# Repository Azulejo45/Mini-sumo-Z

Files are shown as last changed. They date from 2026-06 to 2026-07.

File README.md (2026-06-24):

### ┍━━━━━━━━━━━━»•»  «•«━━━━┑
#   ┕Zangetsu-MiniSumo┙        

### - Proyecto de mini sumo con la capacidad de ser controlado de manera bluetooth y automata. Equipado con 4 sensores:  2 laterales, 1 frontal y uno en la parte inferior, el de piso.
♥

## ..••°°━✦❘༻⋞ 〈 Autores  〉 ⋟༺❘✦━━°°••..

- ⋆ˊˎ-   ┌──༺♥༻❀**Velazquez Joaquim**❀༺♥༻
  
- ⋆ˊˎ-  **Rodriguez Thiago**

### *---16/3/2026---*

♥
## •*¨*•.¸¸☆*･ﾟ Especificaciones generales ﾟ･*☆¸¸.•*¨*•

˚₊· ͟͟͞͞➳❥ Dimensiones del robot: 10 cm x 10 cm x 4,5 cm.

˚₊· ͟͟͞͞➳❥ Consumo total: 7,4V.

˚₊· ͟͟͞͞➳❥ Corriente total: 800mA.

˚₊· ͟͟͞͞➳❥ Material de la carrocería: PLA.

˚₊· ͟͟͞͞➳❥ Peso (aproximado): 300g.
## ✭∞∞∞∞∞∞∞∞✭∞∞•,¸,.·' ✩ '·.,¸,•∞∞✭∞∞∞∞∞∞∞∞✭

♥
## Objetivo del proyecto
### ✩°｡𓂃𓏧︶︶︶︶︶︶︶︶┈୨•♡•୧┈︶︶︶︶︶︶︶𓂃𓏧｡°✩
_El objetivo principal de este proyecto es poner a prueba lo aprendido en años anteriores y este, pudiendo aplicarlo en el proceso de preparacion y  creacion de un robot modelo Mini-Sumo, siguiendo el reglamento de la liga nacional de robotica LNR, para que se encuentre en condiciones en poder participar en una competencia de esta misma_
### ✩°｡𓂃𓏧⌒⌒⌒⌒⌒⌒⌒⌒┈୨•♡•୧┈⌒⌒⌒⌒⌒⌒⌒⌒𓂃𓏧｡°✩
\
\
.
### ∘₊✧───∘₊✧───•-•⟮ ◆ ⟯•-•───✧₊∘───✧₊∘
## ˗ˏˋ ꒰ **Este proyecto fue realizado con algunos componentes en donde se puede llegan a encontrar:** ꒱ ˎˊ˗

- Micro: Esp32 C3 super mini.
 > Memoria: 400 KB SRAM, 4 MB Flash.Conectividad: Wi-Fi (2,4 GHz).\
 > Bluetooth 5.0 LE (Low Energy).\
 > Alimentación: Funciona a 3,3 V con entrada USB-C de 5 V.

- Bateria de Lipo.
 > Almacenamiento: 7,4V.\
 > 2 celdas (3,7V por celda)
  
- Sensor de piso: TCRT5000.
 > Voltaje de operación: 3.3V-5V.\
 > Dimensiones: 31 mm × 13 mm × 2 mm.\
 > Rango de detección: 30° más amplio.

- Sensor detector de obstáculos: HC-sr04.
 > Voltaje de operacion: 5V.\
 > Cantidad de pines: 4.\
 > Distancia de deteccion: 2 a 450cm.
 
- Motores: Micro motores Pololu 250RPM.
 > Dimensiones: 26x10x12mm.\
 > Voltaje de operacion: 6V.\
 > Torque maximo: 333Nm (Newton - metro).

- Puente H: DRV8833.
 > Dimensiones: 4 mm × 18,1 mm × 21,1 mm.\
 > Voltaje de operacion: 2.7V-10.8V.\
 > Corriente máxima de salida: 1,5A.
 ### ∘₊✧───∘₊✧──────✧₊∘───✧₊∘
\
.
## ╔══✬✩══╡˚✧Componentes utilizados✧˚╞══✩✬══╗
- ➸ *Esp32 C3 super mini.*
- ➸ *Bateria de Lipo.*
- ➸ *TCRT5000.*
- ➸ *HC-sr04.*
- ➸ *Micro motores Pololu 250RPM.*
- ➸ *DRV8833.*
## ╚═══*+:｡ . ｡:+*═══✮❁•°❀°•❁✮═══*+:｡ . ｡:+*═══╝
\
\
\
\
\
♥
# Diseño del circuito



## Descripcion del funcionamiento

El minisumo utiliza tres sensores para guiarse, con dos ubicados en los costados; otro en la parte frontal. Cuando un objeto entra en el rango del sensor frontal, el minisumo avanza hasta chocar contra dicho objeto. Esto siempre se cumple hasta que se quite la orden.\
Cuando uno de los sensores en los costados detectan algo cerca, se posiciona para estar de frente al objeto, retrocediendo y girando en direccion paralela a este.
Este mismo, utiliza el sensor de piso para evitar salirse del dohyo, detectyando la franja limite y volviendo para no estar tan vulnerable a cualquier empuje que lo saque de juego.

## Esquematico



## Layout de PCB



# Pasos a seguir para armar el mini-sumo
## ˚*•̩̩͙✩•̩̩͙*˚＊˚*•̩̩͙✩•̩̩͙*˚＊˚*•̩̩͙✩•̩̩͙*˚＊˚*•̩̩͙✩•̩̩͙*˚＊˚*•̩̩͙✩•̩̩͙*˚

### Primero elistaremos las herramientas necesarias para llevar a cabo la placa.

.°-> Un recipiente\
.°-> Percloruro\
.°-> Una agujereadora\
.°-> Una placa de cobre\
.°-> Papel fotografico\
.°-> Tinta Tonel\
.°-> Una impresora(Para imprimir el diseño PCB)\
.°-> Cable USB-C (Para cargar el codigo.)

 ### -|preparación de la placa:

1) Descargar el archivo de PCB de "Zungetosu(MiniSumo).kicad_pcb".\
2). Imprimir el PCB en una hoja fotográfica (como lo son las hojas de revista) con tinta "tonel".\
3) Proceda a planchar el PCB a la placa del lado del cobre.\
4) Revisar que el diagrama del PCB se haya pegado correctamente retirando la hoja fotográfica y cualquier excendete de esta (Utilice agua para remover con facilidad el papel).\
5) Sumergir la placa en un recipiente con percloruro.\
6) Dejarlo descansar un tiempo (Resivar periodicamente el cobre de la placa)\
7) Cuando el cobre se haya disuelto y solo quede el diseño, retirarlo con CUIDADO (Es un liquido corrosivo; dificil de quitar de la ropa).\
8) Limiparlo la placa con agua para quitar el excedente de percloruro.

 ### -|Soldar los componentes en la placa ya hecha en el siguiente orden:
 
1. Capacitores SMD
2. Pineras
3. Borneras
4. Resistencias SMD
5. Regulador AMS1117 5V

 ### Medidas de seguridad.

.°-> El percloruro es un tanto corrosivo, capáz de manchar con facilidad la ropa y otra prendas.\
.°-> Cuando vaya a hacer agujeros en la placa, tiene que ser en una superficie solida. Es probable que la placa pueda salir dispara en una base dispareja o inquieta.\
.°-> Mientra planche, este atento a no quemar completamente el papel. Podria causar un incendio.

### Tipo de soldadura/ensamble

Todos los componentes deben fijados a la placa mendiante "soldadura de ola", el cual se utiliza para componentes de orificio pasante (THT). Los componentes debe ser introducidos desde el lado de la placa lisa y sin diseño,para ser soldados en el cobre que se encuentra del otro lado.
En las pineras que estan direccionadas en horizontal, se debe colocar el ESP32(integrado).
En la pineras que se encuentran en vertical, el DRV8833.

### -|Carroceria

1. Descargar el modelo 3D de la carroceria ubicada en HARDARE.
2. Descargar un modelo 3D de dos braquets y 2 ruedas con un radio de 20mm.
3. Imprimir ambos archivos.
4. Comprar cuatro tornillos para tuerca M3, 6 tuercas M3 y 2 prisioneros M3.
5. Unir la carroseria con los braquets mediante 4 tornillos M3 y 4 tuercas M3.

### -|Codigo

El codigo establece las instrucciones que ejecutara el integrado para poder accionar y manejar al mini-sumo.\
este es bastante simple y considera los 4 sensores teniendo en cuenta que:

.°-> No debe salir del tatami.
.°-> Debe atacar y empujar al otro mini-sumo fuera del area.
.°-> Esquivar al mini-sumo rival cuando se le de la orden.

#### -|Compilacion/Carga

Cuando la placa ya este monatada, se utilizara un cable USB tipo C para conectar el integrado(ESP32) a un ordenador. Mediante el programa [Arduino IDE](https://www.arduino.cc/en/software). Copie el codigo que se encuentra en este repositorio y pueguelo en el programa. En el apartado superior encontrara 4 botones.\
El primero es para verificar si el programa tiene errores\
El segundo es para subir el codigo al integrado\
El tercero no es importante para esto.\
El cuarto es para poder seleccionar la placa y el puerto\
En este ultimo, busque el siguiente modelo: ESP32_C3_SUPER_MINI, y seleccionelo. En caso de no encontrarlo, use el "ESP32 C3 DEV MODULE". Junto a eso, seleccione el puerto USB por el cual esta conectado a su ordenador(Se cuenta de izquierda a derecha).\
Ahora, verifique el codigo por el primero boton de la parte superior. Si marca algun error, copie el codigo entero de nuevo y vuelva a pegarlo./
Una vez verificada la funcionalidad del codigo, utilice el segundo boton presente para poder subir el codigo al integrado de la placa. Si hay alguno otro error durante este proceso, consulte internet.

#### -[Librerias
- Para poner librerias, dirigase al lateral izquierdo de la interfaz de Arduino IDE, y seleccione el tercer boton (que contiene un simbolo con libros).

#### -[Datasheets/Referencias

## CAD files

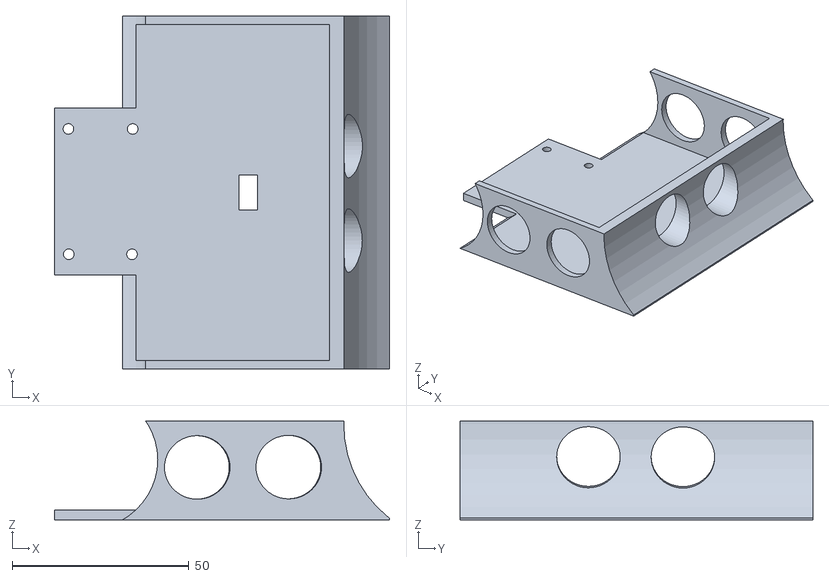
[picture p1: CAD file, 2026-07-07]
CHASIS 3D/carroceria.stl
95.0 x 100.0 x 28.0

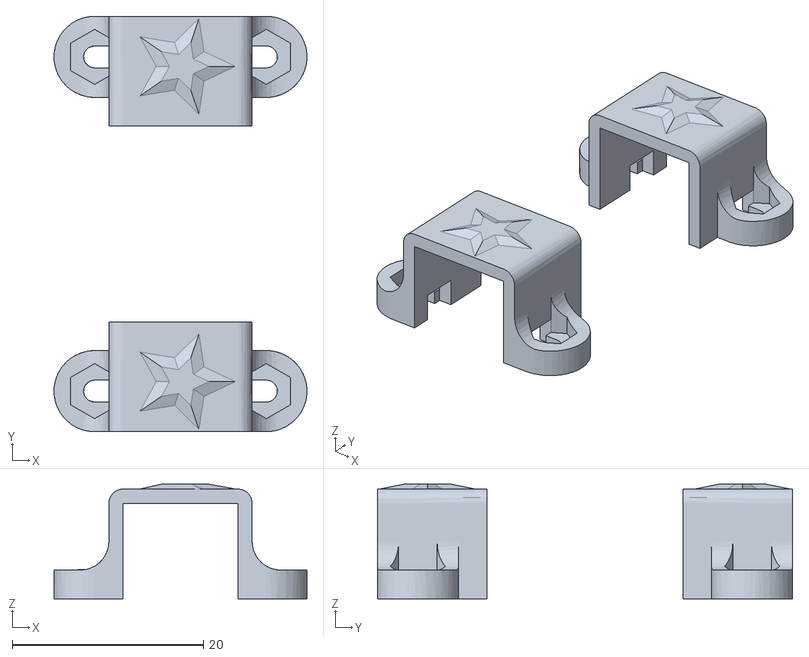
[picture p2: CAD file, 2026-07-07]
CHASIS 3D/carroceria2.stl
26.5 x 43.5 x 12.0

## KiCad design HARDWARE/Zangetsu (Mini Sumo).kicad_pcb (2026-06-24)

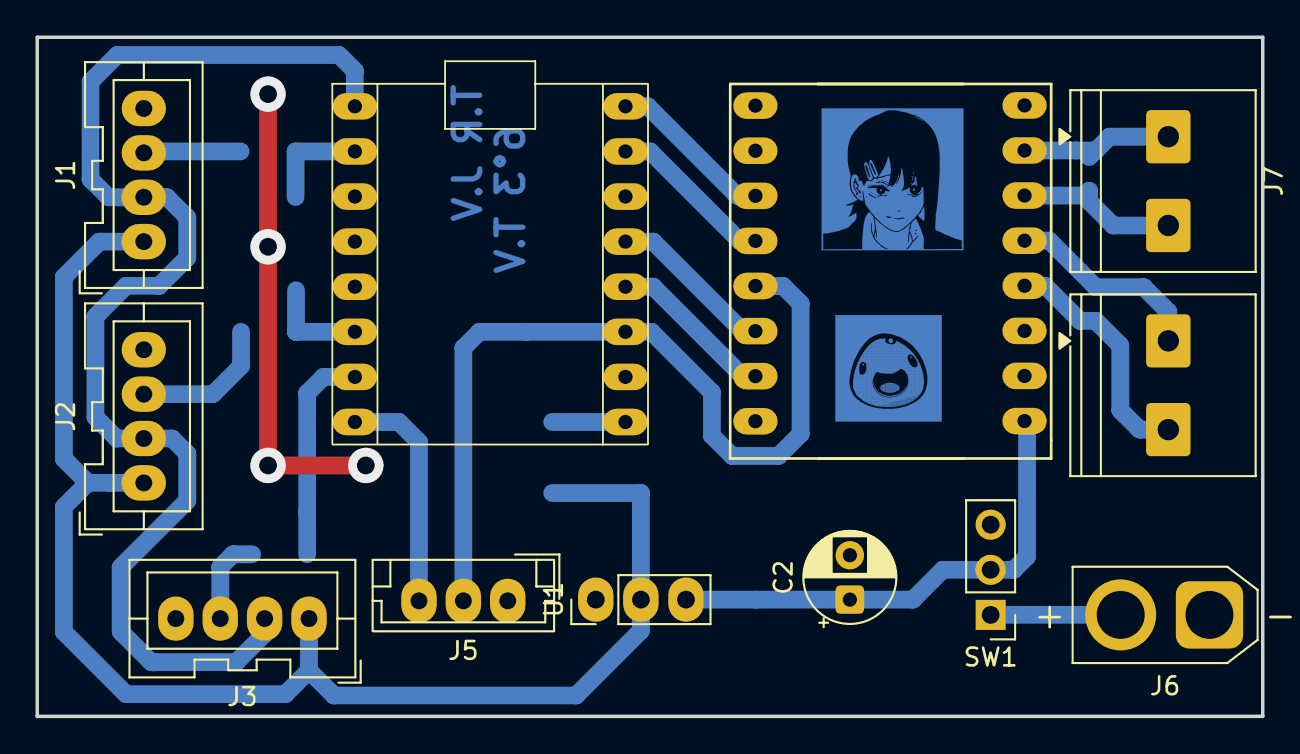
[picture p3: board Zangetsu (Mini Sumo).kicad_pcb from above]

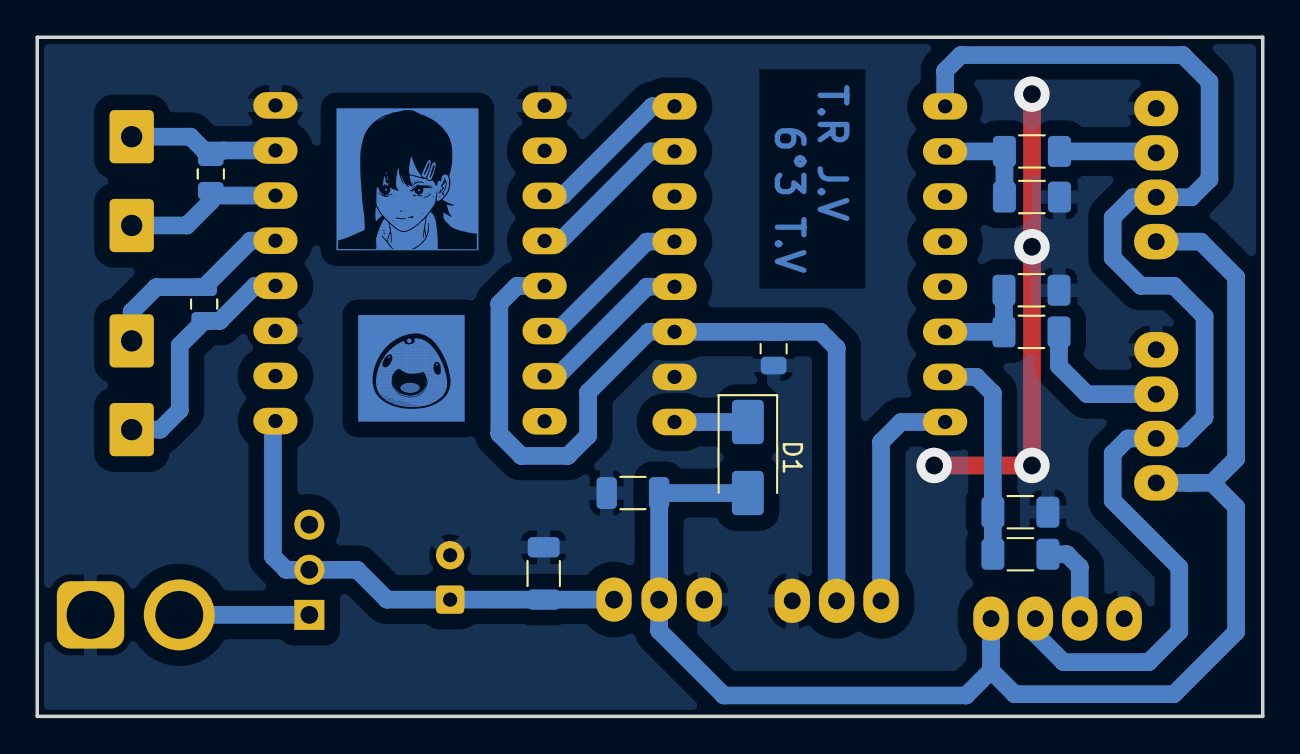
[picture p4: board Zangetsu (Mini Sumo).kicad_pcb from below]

Board: 2 copper layers, 69.0 x 38.2 mm, 24 parts (12 on the bottom side), 22 nets.

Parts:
C1, C4, C6: 100nF; C_0805_2012Metric
C2: 100uF; CP_Radial_D5.0mm_P2.50mm
C3, C5: 10uF; C_1206_3216Metric
D1: 1N4007; D_SMA
DRV1: DRV8833_Pololu
ESP32_C3_SM1: ESP32_C3_SM
J1, J2, J3: JST_XA_B04B-XASK-1_1x04_P2.50mm_Vertical
J4, J7: TerminalBlock_Philmore_TB132_1x02_P5.00mm_Horizontal
J5: JST_EH_B3B-EH-A_1x03_P2.50mm_Vertical
J6: AMASS_XT30U-F_1x02_P5.0mm_Vertical
R1, R4, R6: 2k; R_1206_3216Metric_Pad1.30x1.75mm_HandSolder
R2, R3, R5: 1k; R_1206_3216Metric_Pad1.30x1.75mm_HandSolder
SW1: SW_DPST_x2; PinHeader_1x03_P2.54mm_Vertical
U1: AMS1117; PinHeader_1x03_P2.54mm_Vertical

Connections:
+3.3V: C1.2, DRV1.13 (STBY), ESP32_C3_SM1.11 (3V3), J5.2
+5V: C5.1, D1.2 (A), J1.1, J2.1, J3.1, U1.2 (VO)
/ECHO1: ESP32_C3_SM1.2 (GPIO6), R1.2, R2.2
/ECHO2: ESP32_C3_SM1.6 (GPIO10), R3.2, R4.2
/ECHO3: ESP32_C3_SM1.7 (GPIO20), R5.2, R6.2
/IN1: DRV1.15 (AIN2), ESP32_C3_SM1.12 (GPIO4)
/IN2: DRV1.14 (AIN1), ESP32_C3_SM1.13 (GPIO3)
/IN3: DRV1.12 (BIN1), ESP32_C3_SM1.15 (GPIO1)
/IN4: DRV1.11 (BIN2), ESP32_C3_SM1.16 (GPIO0)
/M1: C4.2, DRV1.4 (AO1), J4.2
/M2: C4.1, DRV1.5 (AO2), J4.1
/M3: C6.1, DRV1.7 (BO1), J7.1
/M4: C6.2, DRV1.6 (BO2), J7.2
/OUT: ESP32_C3_SM1.8 (GPIO21), J5.3
/TRIGGER: ESP32_C3_SM1.1 (GPIO5), J1.2, J2.2, J3.2
GND: C1.1, C2.2, C3.1, C5.2, DRV1.3 (GND), DRV1.8 (GND), DRV1.9 (GND), ESP32_C3_SM1.10 (GND), J1.4, J2.4, J3.4, J5.1, J6.1, R1.1, R4.1, R6.1, U1.1 (ADJ)
unnamed: D1.1 (K), ESP32_C3_SM1.9 (5V)
unnamed: J1.3, R2.1
unnamed: J2.3, R3.1
unnamed: J3.3, R5.1
unnamed: J6.2, SW1.1 (A)
VCC: C2.1, C3.2, DRV1.1 (VM), SW1.2 (B), U1.3 (VI)
